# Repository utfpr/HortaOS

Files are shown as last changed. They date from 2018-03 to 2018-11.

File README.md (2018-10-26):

# For English, click [HERE](https://github.com/utfpr/HortaOS/blob/master/README_EN.md) or read the README_EN.md file!

# Controlador Automático Para Horta Comunitária
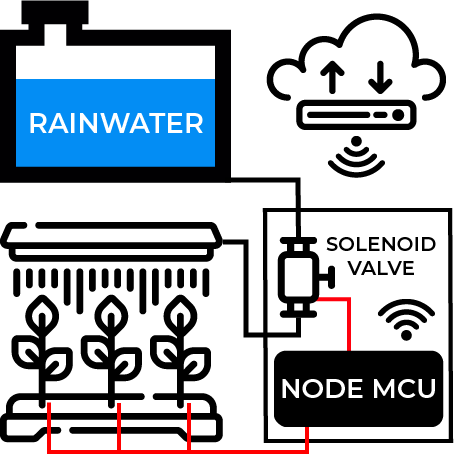
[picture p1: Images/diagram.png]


Controlador automático baseado em um controlador Node MCU que controla a irrigação baseado na umidade do solo que registra os logs de umidade, fluxo de água, e temperatura do solo na plataforma ThingSpeak. Desenvolvido pela Universidade Tecnológica Federal do Paraná, Campus Campo Mourão, sob supervisão do Professor Ivanilton Polato.

## Itens Necessários
Para montar este controlador, você vai precisar dos seguintes items:
1. Node MCU
2. Válvula Solenóide
3. Sensor de Fluxo
4. Sensor de umidade do solo
5. Sensor de temperatura DS18B20
6. Módulo Relé 5v
7. Regulador de tensão L7805CV
8. Fonte 12v
9. Resistor 220Ω
10. 2 Cotovelos de cano 3/4" para mangueira
12. Luva 3/4" com rosca
13. Conta no ThingSpeak
14. Arquivo ```Modelo 3D.obj``` impresso

## Esquema para montagem
Para realizar a montagem do controlador, você deverá seguir o esquema abaixo. Caso prefira, o projeto do Fritzing também está disponível para download neste repositório.

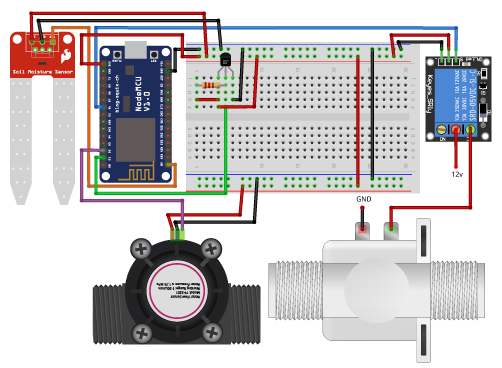
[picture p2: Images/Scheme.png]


## Configuração da IDE do Arduino para o NodeMCU
Entre na IDE do Arduino e clicar em **Arquivo -> Preferências**:



Na tela seguinte, digite o link abaixo no campo URLs adicionais de Gerenciadores de Placas:

http://arduino.esp8266.com/stable/package_esp8266com_index.json

A sua tela ficará assim:



Clique em OK para retornar à tela principal da IDE

Agora clique em Ferramentas -> Placa -> Gerenciador de Placas:



Utilize a barra de rolagem para encontrar o esp8266 by ESP8266 Community e clique em INSTALAR



Após alguns minutos as placas da linha ESP8266 já estarão disponíveis na lista de placas da IDE do Arduino.

(Tutorial por [FilipeFlop](https://www.filipeflop.com/blog/programar-nodemcu-com-ide-arduino/))

## Upload do código
Após realizar o passo anterior, você deverá alterar algumas variáveis. São elas:

1. ```SSID_WIFI```
2. ```PSWD_WIFI```
3. ```WriteKey```

**SSID_WIFI:** é a variável que armazena o nome da rede Wifi que o NodeMCU vai se conectar

**PSWD_WIFI:** é a variável que armazena a senha da rede WIFI

**WriteKey:** Guarda a chave de escrita para o ThingSpeak

Após realizar essas alterações, você poderá enviar o arquivo ```HortaOS.ino``` para o Node MCU. 

## Montagem Final
Para montagem final, foi feito um molde 3D para impressão separados em dois modulos. Sendo um deles para o microcontrolador e o outro para parte onde será instalado o solenóide e o sensor de fluxo.
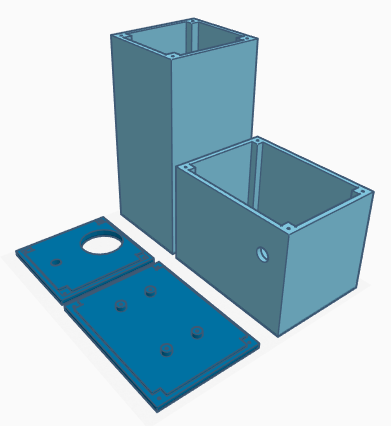
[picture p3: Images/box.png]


### Alimentação
Não pe possível alimentar o Node MCU com 12v diretos da fonte, então para isso, utilizamos o ```L7805CV``` para reduzir a alimentação da fonte para 5v.

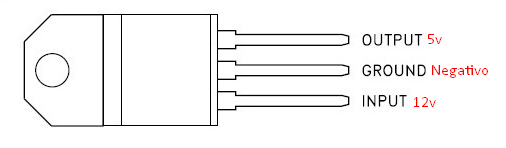
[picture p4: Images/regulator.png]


Com isso, basta ligar os 5v no ```VIN``` do Node MCU e o negativo no ```GROUND```

### Montagem da parte hidraulica
Para montar esta parte, é necessário dos itens ```2```, ```3```, ```12``` e ```13```. Basta seguir o esquema de montagem da imagem abaixo

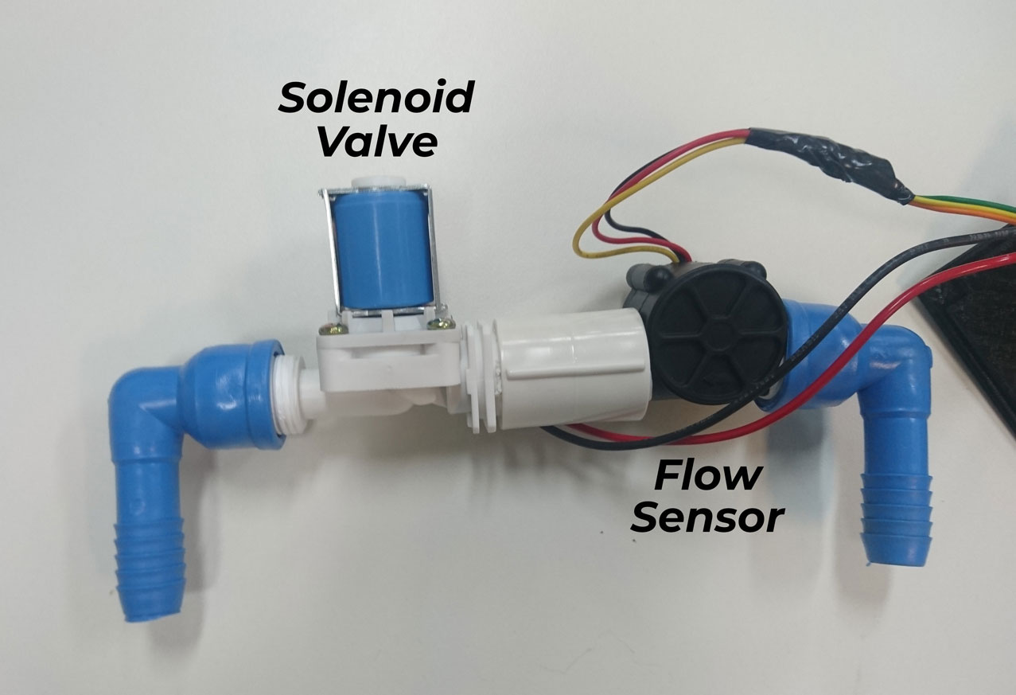
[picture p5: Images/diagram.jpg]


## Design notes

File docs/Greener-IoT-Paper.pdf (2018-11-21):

# Greener IoT: Rainwater Sustainable Green and Vegetable School Gardens

Abstract
We describe here our research efforts towards the development and popularization of a prototype for sustainable vegetable gardens automation at schools in Campo Mourão, Paraná, Brazil. Our research is focused on low cost Internet of Things components that can optimize the water use on green and vegetable gardens, especially on public schools, allowing the use of rainwater for irrigation. We also concentrate our efforts in the minimization of the components cost, facilitating the access to the system by schools, and even communities, with budget restrictions. Our initial efforts have showed the feasibility of the project by the development of a complete functional prototype, and its application on a research green garden at our university campus. Next steps include the prototype refinement, and application on selected public schools and communities.

Author Keywords
IoT; Green and vegetable gardens; Rainwater usage; Public schools; Communities; Budget restrictions.

ACM Classification Keywords
- Computer systems organization~Embedded systems
- Applied computing~Agriculture

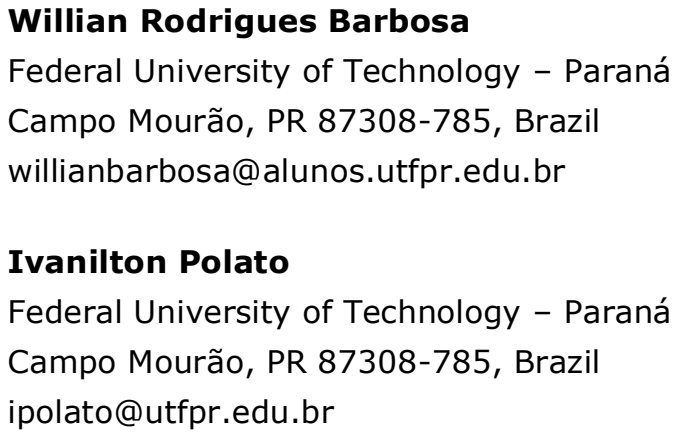
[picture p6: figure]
Willian Rodrigues Barbosa; Campo Mourão, PR 87308-785, Brazil willianbarbosa@alunos.utfpr.edu.br; Ivanilton Polato; Campo Mourão, PR 87308-785, Brazil ipolato@utfpr.edu.br

Federal University of Technology – Paraná

Federal University of Technology – Paraná

Our Context
The evolution and growth in the use of mobile platforms with the Internet of Things (IoT) technologies, allied to Cloud Computing and Big Data popularization, poses as a viable way of promoting concepts such as sustainability and quality of life, inherent concepts of our modern society.

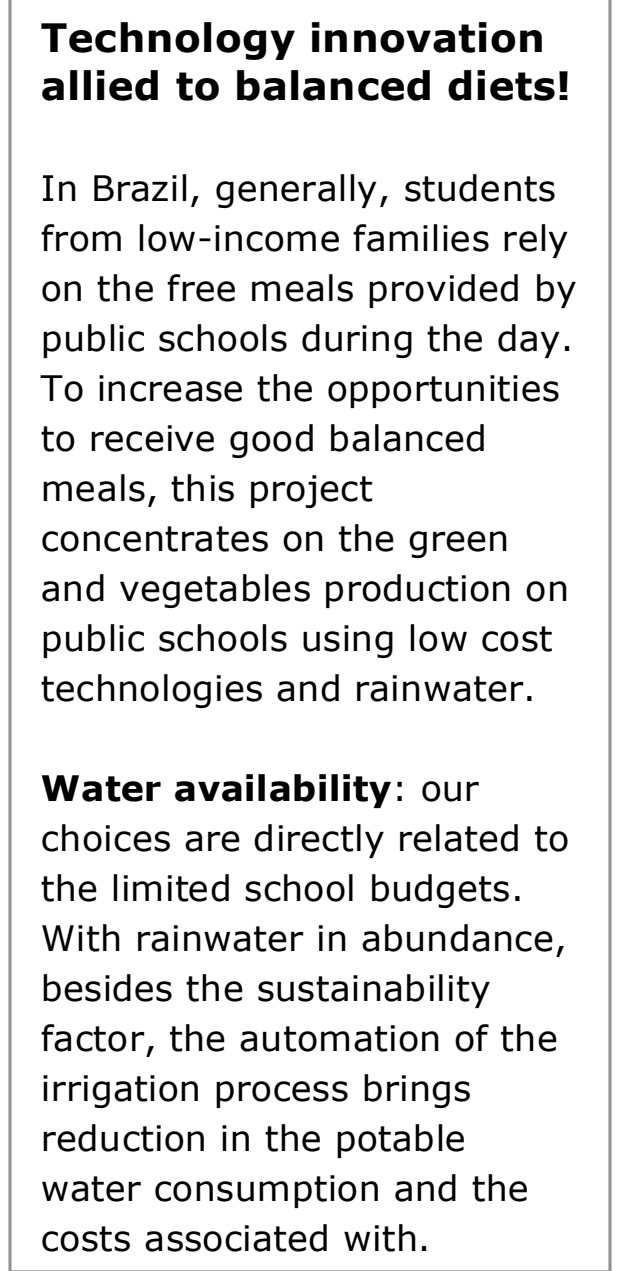
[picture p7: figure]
Technology innovation allied to balanced diets!; In Brazil, generally, students from low-income families rely on the free meals provided by public schools during the day. To increase the opportunities to receive good balanced meals, this project concentrates on the green and vegetables production on public schools using low cost technologies and rainwater.; Water availability: our choices are directly related to the limited school budgets. With rainwater in abundance, besides the sustainability factor, the automation of the irrigation process brings reduction in the potable water consumption and the costs associated with.

Given an IoT scenario, where a set of thousands of intelligent and distributed devices work in a coordinated and interconnected fashion, raising the society's awareness to the benefits of using such technologies as a natural resource management tool is feasible and necessary.

Water is one of the most precious natural resource today. Considering the water distribution, which is certainly uneven across the planet, the rational use of such resource is mandatory nowadays. The sustainable water use relies on the population awareness and, more recently, on the technology enhancements [1]. In this context, water irrigation raises as one important problem in today’s society, where the efficient production of food is highly desired.

According to the Brazilian’s National Water Agency [2], irrigation in Brazil is responsible for 46% of the water used from hydric resources, and responds for 67% of the total water used in the country. The same agency proposes policies on the water used for irrigation and argue that efficient natural resource usage can bring long-term benefits, which includes the increase in food production, overall production cost reduction, and sustainable natural resources reuse.

Therefore, the options for sustainable water use are always in constant development. This research focuses on the reuse of rainwater to irrigate small vegetable gardens as a way to promote (1) water reuse and sustainability awareness, and (2) IoT technology dissemination on primary schools and small neighborhoods or communities.

Our Research
We designed and assembled an automated irrigation system that uses a rainwater cistern to irrigate a green and vegetable garden. This project is under development as part of the social interaction between our university and public schools by means of a community project.

Our prototype was developed using an Arduino based platform, the Node MCU, which also includes an ESP8266 Wi-Fi shield onboard. The prototype was designed having as the major goal the component cost minimization. All electronic parts will need a total budget of approximately US$20. If we include the dripping pipes and hoses that take water across the garden, we will need another US$15 to US$20. Although there are more precise sensors, this would increase the overall budget and the results would be roughly the same, since we do not target precise agriculture irrigation. All the selected parts and components are easily available, including the electronics. All listing, assembly schematics and source code are available at our GitHub repository [3]. All documents and codes developed are released under an open source software license.

The prototype is fully functional and, at this point, is under testing at our local vegetable garden in the university, controlled by our research group students. All the green and vegetables produced during experimental phase are distributed for free to the community.

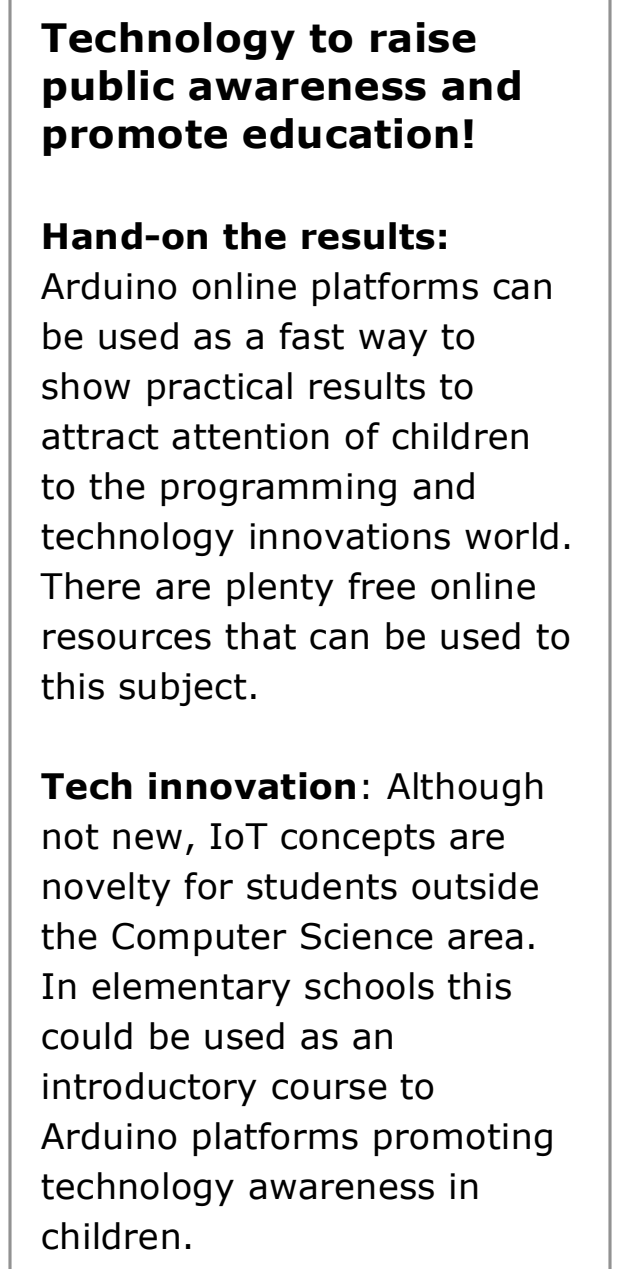
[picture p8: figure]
Technology to raise public awareness and promote education!; Hand-on the results: Arduino online platforms can be used as a fast way to show practical results to attract attention of children to the programming and technology innovations world. There are plenty free online resources that can be used to this subject.; Tech innovation: Although not new, IoT concepts are novelty for students outside the Computer Science area. In elementary schools this could be used as an introductory course to Arduino platforms promoting technology awareness in children.

Technology Dissemination
Although Arduino-based irrigation systems are not new, they are easy projects to replicate, with hands-on and fast results that attract people outside de Computer Science community. Once we finish the testing phase in the university campus, our goal is to replicate the project in selected public elementary schools from Campo Mourão.

The selected schools will be responsible for purchasing the parts to assembly the irrigation device, provide a cistern which can hold the water used for the vegetable garden, and select groups of students that will take part in the project. That is the main reason to keep a low overall budget to replicate the project. Thus, the Arduino was the first choice due to its capacities, flexibility and dissemination in the IoT community, and certainly, the low cost of the parts and sensors.

Our research group will be responsible for the teaching course to introduce the technologies for teachers and children in the target schools. We expect that participant groups assembly their own prototypes thoughout the course. We will primarly focus on the hardware assembly, since the software development would require skills that our participants might not have. At first, we will use our own software in the prototype.

In this context, the fast practical results will serve as leveraging tool to introduce basic, computer science and IoT concepts in elementary schools as a technology dissemination platform. The basic course will be made available online using the Moodle platform. Additionally, we expect that this could help the dissemination of introdutory programming courses in the early shool years, which is rare in Brazilian elementary schools, especially in public schools. Arduino is such a flexible platform that would allow the development of interesting practical applications, using free online tools such as Sketch [4] and ArduBlock [5].

Gathering and Using Data
Another important part of the project replication in schools is the data gathered. Our prototype keeps records in the ThingSpeak platform. The collected data about soil humidity and temperature might help in the refinement of the irrigation process, providing feedback about the water consumption for different green and vegetables. Teachers in Science classes could use the data to illustrate differences between agricultural cultures. Water cycle, use and reuse awareness could also be explored themes. ThingSpeak is a user-friendly platform, allowing easy data analysis, providing several mechanisms to visualize the data collected. This would serve as proxy to train elementary teachers to use technology to favor experimental classes.

LATAM CSCW Challenges and Opportunities Most of our primary challenges here in Brazil are related to budget and bureaucracy. Our research scenario relies, most of the times, on limited reserch budget to develop and to apply the results. Our technology innovation popularization faces problems with bureaucracy.

Nevertheless, research opportunities include raising public awareness on several sustainability topics, including social and environmental aspects of everyday life. The Internet of Things technologies broadened our possibilities, including the smart cities agenda. Our research group has potential interest in efforts towards energy consumption management on IoT devices. This includes several scenarios including urban mobility, environmental monitoring, including green urban areas and pollution levels. In these opportunities, IoT devices are distributed in a large area, performing remotely monitoring tasks.

Additionally, the application of the STEM methodology concepts in the project replication is an extra collaboration opportunity. This could bring students and teachers closer to the project, providing resources for adaptation and overall solution improvement according to restrictions or specific needs.

We also claim that collaboration comes from sharing artifacts and communicating the results. Thus, all of our developed artifacts are released under open licenses: software is released under permissive open source licenses; other artifacts generally use a Creative Commons license. These simple actions allow popularization and collaboration on the project.

References

[1] CARVALHO, D. F. D. et al. Water use efficiency and economic return of fresh vegetable in organic cultivation. Revista Brasileira de Engenharia Agrícola e Ambiental, v. 20, p. 637-642, Jul. 2016. ISSN: 1415-4366.
[2] Agência Nacional de Águas. ATLAS IRRIGAÇÃO: Uso da Água na Agricultura Irrigada, 2016. Available at: http://atlasirrigacao.ana.gov.br.
[3] BARBOSA, W.; POLATO, I. Horta OS Repository, 2018. Available at: http://github.com/utfpr/HortaOS
[4] MIT Media Lab. Scratch, 2013. Available at: http://scratch.mit.edu/
[5] LI, D.; QICHEN, H. ArduBlock, 2011. Available at: http://blog.ardublock.com/

Short Bio
Ivanilton Polato is a professor at the Federal University of Technology – Paraná. He completed his PhD at the University of São Paulo researching energy consumption analysis on distributed computing platforms. His main interests are related to green computing and energy consumption on computing platforms, including IoT systems; open source programming, repositories and licenses. Recently, he has dedicated efforts towards topics regarding mining software repositories and social platforms such as GitHub.

Willian Rodrigues Barbosa is an undergraduate student at the Federal University of Technology – Paraná, member of this project as developer and collaborator.

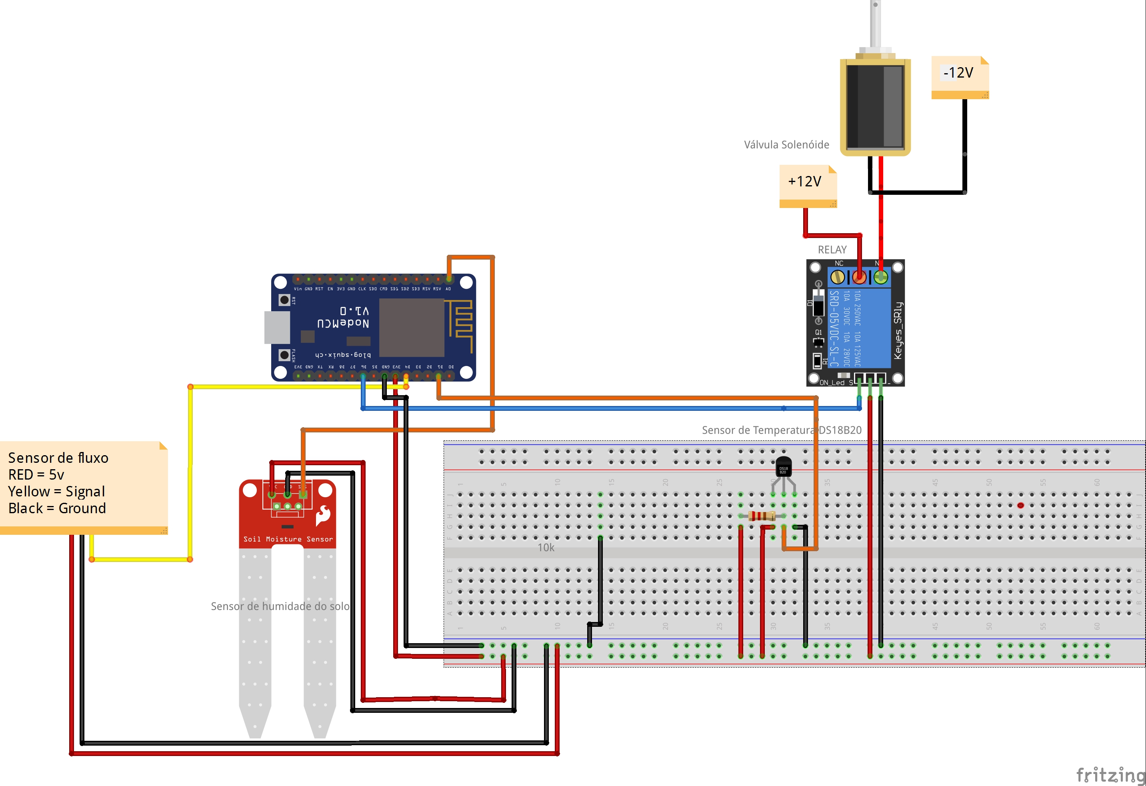
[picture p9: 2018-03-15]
Images/scheme.jpg

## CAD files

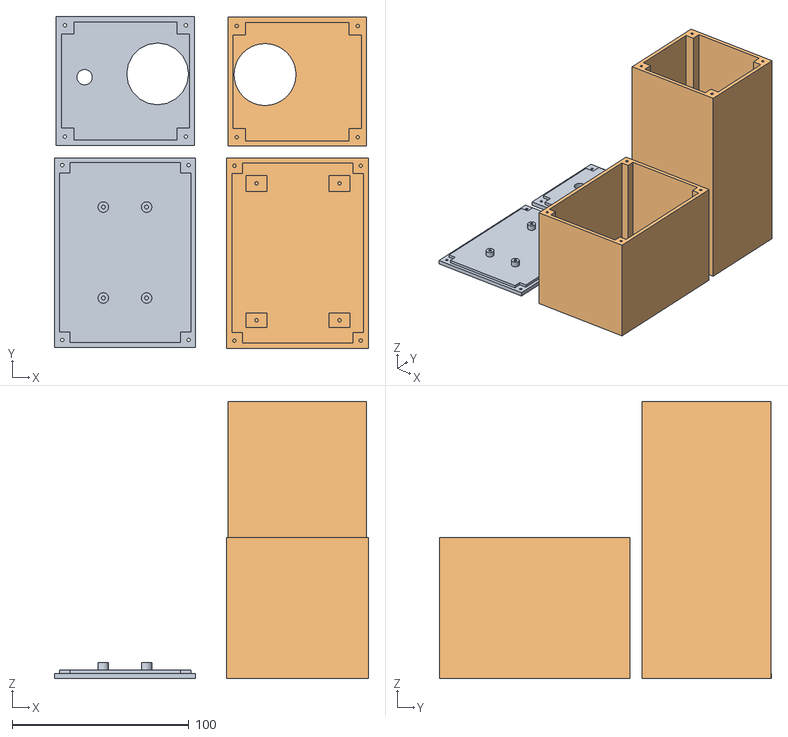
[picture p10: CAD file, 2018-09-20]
Modelo 3D.obj
178.0 x 188.0 x 157.0

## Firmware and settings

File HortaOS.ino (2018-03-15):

#include <DallasTemperature.h>
#include <OneWire.h>
#include <ESP8266WiFi.h>

//defines
#define SSID_WIFI "INSIRA O NODE DA REDE WIFI AQUI"    // Nome da rede wifi a ser conectada
#define PSWD_WIFI "INSIRA A SENHA DA REDE WIFI AQUI"       // Senha da rede wifi a ser conectada
#define SEND_DELAY 30000            // Intervalo de post ao ThingSpeak
#define HUM_SENSOR A0               // Define o pino A0 como entrada do sensor de humidade do solo
#define RELAY_PIN 12                // Define o pino do Relay (Pino D6)
#define ONE_WIRE_BUS 5              // Define o pino do sensor de temperatura (Pino D1)
#define SENSOR_INTERRUPT 2;         // Define interrupção (Pino D4)
#define FLOW_SENSOR 2;              // Define o sensor de fluxo (Pino D4)

#define DRY 50        // DEFINE QUANDO O RELE VAI SER ATIVADO
#define WET 70        // DEFINE QUANDO O RELE VAI SER DESATIVADO

char ThingSpeakAPI[] = "api.thingspeak.com";         // Define o endereÃ§o da api do ThingSpeak
String WriteKey = "INSIRA A CHAVE DE ESCRITA DO THINGSPEAK";                // Define a chave da api de escrita
long lastConnectionTime;                             // Variável que guarda o tempo da ultima conexÃ£o com a api
bool irrigationStatus = false;                       // Variável define o status da irrigaÃ§Ã£o
int iStatus = 0;                                     // Variável auxiliar para irrigação
WiFiClient client;                                   // Define o cliente Wifi

void SendInfo(String Data);             // ProtÃ³tipo da funÃ§Ã£o de envio ao ThingSpeak
void ConnectWiFi(void);                 // ProtÃ³tipo da funÃ§Ã£o que conecta a board a rede Wifi
int ReadHum(void);                      // FunÃ§Ã£o que lÃª a humidade do solo e retorna um valor entre 0 e 100 (Porcentagem)

// Fator de calibração (Número de pulsos gerados pelo sensor por cada litro)
float calibrationFactor = 4.5;

// Contador de pulso
volatile byte pulseCount;  

float flowRate;
unsigned int flowMilliLitres;
unsigned long totalMilliLitres;

unsigned long oldTime;
unsigned long loopTime;                   // Guarda o tempo de clock do ciclo

OneWire oneWire(ONE_WIRE_BUS);            // Define uma instancia do oneWire para comunicacao com o sensor

/*
   FunÃ§Ã£o envia informaÃ§Ãµes ao ThingSpeak
   Recebe por parametro a string de dados a serem enviados ao canal no ThingSpeak
   NÃ£o retorna nenhum valor
*/
void SendInfo(String Data)
{
  if (client.connect(ThingSpeakAPI, 80)) // Conecta com a api do ThingSpeak na porta 80
  {
    //faz a requisiÃ§Ã£o HTTP ao ThingSpeak
    client.print("POST /update HTTP/1.1\n");
    client.print("Host: api.thingspeak.com\n");
    client.print("Connection: close\n");
    client.print("X-THINGSPEAKAPIKEY: " + WriteKey + "\n");
    client.print("Content-Type: application/x-www-form-urlencoded\n");
    client.print("Content-Length: ");
    client.print(Data.length());
    client.print("\n\n");
    client.print(Data);

    lastConnectionTime = millis();      // Define o tempo de ultima conexÃ£o para o momento atual
    Serial.println("Status: Valor enviado para a API");
  }
}

/*
   FunÃ§Ã£o faz a conexÃ£o com a rede wifi
   NÃ£o tem parametro
   NÃ£o retorna nenhum valor
*/
void ConnectWiFi(void)
{
  client.stop();                                  // Para o cliente para efetuar nova conexÃ£o
  Serial.println("Conectando-se Ã  rede WiFi...");
  Serial.println();
  delay(1000);                                    // Tempo de espera atÃ© a conexÃ£o
  WiFi.begin(SSID_WIFI, PSWD_WIFI);               // Conecta a rede previamente definida

  while (WiFi.status() != WL_CONNECTED)           // Aguarda atÃ© a conexÃ£o ser efetuada
  {
    delay(500);
    Serial.print(".");
  }

  Serial.println("");
  Serial.println("WiFi connectado com sucesso!");
  Serial.println("IP obtido: ");
  Serial.println(WiFi.localIP());                 // Printa o ip obtido pela board
  delay(1000);
}
/*
    FunÃ§Ã£o para leitura e processamento da humidade do solo obtida pelo sensor na porta A0
    NÃ£o tem parametros
    Retorta um valor entre 0 e 100 (porcentagem)
*/

DallasTemperature sensors(&oneWire);
DeviceAddress sensor1;


void pulseCounter()
{
  // Increment the pulse counter
  pulseCount++;
}
void mostra_endereco_sensor(DeviceAddress deviceAddress)
{
  for (uint8_t i = 0; i < 8; i++)
  {
    // Adiciona zeros se necessário
    if (deviceAddress[i] < 16) Serial.print("0");
    Serial.print(deviceAddress[i], HEX);
  }
}



float ReadHum(int sensorValue)
{
  sensorValue = constrain(sensorValue, 475, 1023);  // 495 Define o piso e o teto do valor obtido no sensor
  float soil = map(sensorValue, 475, 1023, 100, 0); // 495 Faz o calculo da porcentagem da humidade com base na leitura do sensor
  Serial.print("Umidade do solo: ");               //
  Serial.print(soil);                               // Printa o valor, somente para fins de desenvolvimento
  Serial.println("%");                              //
  return soil;                                      // Retorna a porcentagem de humidade do solo
}

void setup()
{
  Serial.begin(9600);
  sensors.begin();
  Serial.println("Localizando sensores DS18B20");
  Serial.print("Foram encontrados ");
  Serial.print(sensors.getDeviceCount(), DEC);
  Serial.println(" sensores.");
  if (!sensors.getAddress(sensor1, 0))
    Serial.println("Sensores nao encontrados !");
  // Mostra o endereco do sensor encontrado no barramento
  Serial.print("Endereco sensor: ");
  mostra_endereco_sensor(sensor1);
  Serial.println();

  pinMode(FLOW_SENSOR, INPUT);
  digitalWrite(FLOW_SENSOR, HIGH);

  pulseCount        = 0;
  flowRate          = 0.0;
  flowMilliLitres   = 0;
  totalMilliLitres  = 0;
  oldTime           = 0;

  pinMode(RELAY_PIN, OUTPUT);       // Define o pino do relay como saida
  digitalWrite(RELAY_PIN, LOW);     // Marca o Relay como desligado
  attachInterrupt(SENSOR_INTERRUPT, pulseCounter, FALLING);

  lastConnectionTime = 0;          // Defina o tempo da ultima conexÃ£o em 0
  ConnectWiFi();                   // Efetua a conexÃ£o a rede wifi
  Serial.println("HortaOS READY"); // Infoma no console que o sistema esta pronto
  Serial.println("");
  Serial.println("");
}

//loop principal
void loop()
{
  if((millis() - oldTime) > 1000)    // Only process counters once per second
  { 
    detachInterrupt(SENSOR_INTERRUPT);
    flowRate = ((1000.0 / (millis() - oldTime)) * pulseCount) / calibrationFactor;
    oldTime = millis();
    flowMilliLitres = (flowRate / 60) * 1000;
    totalMilliLitres += flowMilliLitres;
      
    unsigned int frac;
    
    // Print the flow rate for this second in litres / minute
    Serial.print("Fluxo: ");
    Serial.print(int(flowRate));  // Print the integer part of the variable
    Serial.print(".");             // Print the decimal point
    // Determine the fractional part. The 10 multiplier gives us 1 decimal place.
    frac = (flowRate - int(flowRate)) * 10;
    Serial.print(frac, DEC) ;      // Print the fractional part of the variable
    Serial.print("L/min   ||   ");
    // Reseta o contador de pulso para o proximo loop
    pulseCount = 0;
    attachInterrupt(SENSOR_INTERRUPT, pulseCounter, FALLING);
  }

  
  char FieldThingSpeak[50];  // String para armazenar a concatenaÃ§Ã£o de informaÃ§Ãµes
  sensors.requestTemperatures();
  float tempC = sensors.getTempC(sensor1);
  Serial.print("Temperatura do solo: ");
  Serial.print(tempC);
  Serial.print(" C   ||  ");

  float soil, light;                              // Variavel que vai receber a porcentagem da humidade do solo
  soil = ReadHum(analogRead(A0));         // Chama a função que retorna a porcentagem da humidade do solo
  if (soil > DRY && soil < WET && irrigationStatus == true) {
    Serial.println("Status: Irrigacao em andamento");
  }
  else if (soil <= DRY && irrigationStatus == false) { // Verifica se o solo esta seco e então liga o relay
    irrigationStatus = true;
    digitalWrite(RELAY_PIN, LOW);
    Serial.println("Status: Irrigação ligada");
  }
  else if (soil > WET && irrigationStatus == true) { // Verifica se o solo esta molhado e a irrigação esta ligada
    Serial.println("Status: Irrigação desligada");
    irrigationStatus = false;
    digitalWrite(RELAY_PIN, HIGH);
  }

  //Faz a verificaÃ§Ã£o se a board esta conectada a rede e se deve enviar informaÃ§Ãµes ao thingspeak
  if (millis() - lastConnectionTime > SEND_DELAY)
  {
    if (irrigationStatus == true) {
      iStatus = 1;
    } else {
      iStatus = 0;
    }
    sprintf(FieldThingSpeak, "field1=%.2f&field2=%.2f&field3=%d&field4=%.2f", soil, tempC, iStatus, flowRate); // Concatena as informaÃ§Ãµes dentro de uma unica string
    SendInfo(FieldThingSpeak);                   // Chama funÃ§Ã£o que envia as informaÃ§Ãµes ao ThingSpeak
  }
  delay(1000);
}

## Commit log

2018-03-15 Primeiro commit
    Enviado codigo base do projeto e esquema de montagem
    [Esquema de montagem.fzz]
2018-03-15 Modelo para impressão 3D
    Modelo para impressão 3D para montagem final do projeto
2018-09-20 Adiciona modelo 3d da caixa
    [Modelo 3D.obj]
2018-09-25 Adiciona imagem do regulador de tensão
2018-09-25 Adiciona detalhes de montagem no readme
2018-09-27 Adiciona esquema de montagem do solenoide e do sensor de fluxo
2018-09-27 Adiciona instruções de montagem da parte hidráulica
2018-10-06 Adiciona link para a versão em inglês
